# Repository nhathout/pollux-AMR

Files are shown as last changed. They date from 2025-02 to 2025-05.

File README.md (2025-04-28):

# Pollux-AMR · Autonomous Counter-Top Cleaning Robot


> **Last verified:** 27 Apr 2025  
> **Target HW:** Raspberry Pi 4 Model B (4 GB)  
> **Target OS:** Ubuntu 20.04 LTS (headless) with ROS Noetic  

Pollux-AMR is a ROS-driven mobile robot that patrols a kitchen countertop, disinfecting
the surface with a UV-C LED strip while staying clear of cliffs and obstacles.
The original project used a rules-based brain; we now train a real-time PPO agent
on-board via **rl_brain_node.py** for continuous improvement.

---

## 1 · Boot-Up  
    ① Flash Ubuntu 20.04 to the µSD card, boot once to expand the FS
    ② SSH in and run:
    git clone https://github.com/nhathout/pollux-AMR.git
    cd pollux-AMR
    chmod +x setup_env.sh && ./setup_env.sh
    ③ Reboot (systemd service now auto-starts every node)

*Need only a demo video?*
- Links to video demonstrations of Pollux's major functionalities (UV indicator LED, cliff detection, and obstacle avoidance):
    - **UV indication & cliff detection:** [click here](https://drive.google.com/file/d/1kTDrHVp9VE7UjMdm_vTjpf8ZEP2LUoZp/view?usp=sharing)
    - **Obstacle Avoidance:** [click here](https://drive.google.com/file/d/1ax3cWRlPb4nttXV8eBDei8ND6SfjERsN/view?usp=sharing)<br><br>

---

## 2 · Current State (Apr 2025)

| Sub-system | Status | Gotchas & Quirks |
|---|---|---|
| Sensor I/O (hw_publisher.py & hw_publisher_2.py) | ✅ stable | Uses **BCM** pin numbers; wrong ECHO wiring can fry GPIOs. |
| Motor driver (motor_cmd_node.py) | ✅ stable | H-bridge inrush >1 A; keep a 2 A buck or Pi browns out. |
| LED safety (led_gyro_node.py) | ✅ stable | IMU IRQ sometimes locks; power-cycle to clear. |
| RL brain (rl_brain_node.py) | 🟡 beta | Seems to work and learn; first 100 s policy is random. |
| Service file (pollux-robot.service) | ✅ stable | Update **WorkingDirectory=** if you move the repo. |

---

## 3 · Things We Wish We Knew Earlier
1. Ultrasonic crosstalk → fire downward sensors 50 ms apart.  
2. RAM-starved RL → set SWAP = 1024 MB.  
3. Clock drift hurts reward timer → run *timedatectl set-ntp true*.  
4. Wi-Fi sleep kills SSH → set *wifi.powersave = 2* in NetworkManager.  
5. The best power supply for the job.

---

## 4 · Recommended Next Steps

| Area | Content |
|---|---|
| Mechanical | Switch to 12 V steppers for torque & battery life. |
| CV / DL | Add Pi Cam 3 + YOLO-Nano for obstacle detection. |
| DevOps | Stream TensorBoard via MQTT → Grafana. |
| Research | 24 h on-board RL study → short research paper. |

---

## 5 · Directory Map
    pollux-AMR/
    ├─ hardware/
    ├─ images/
    ├─ nodes/
    │   ├─ hw_publisher.py
    │   ├─ hw_publisher_2.py
    │   ├─ motor_cmd_node.py
    │   ├─ led_control_node.py
    │   ├─ led_gyro_node.py
    │   └─ rl_brain_node.py
    ├─ launch/
    ├─ models/
    ├─ scripts/
    └─ systemd/

---

## 6 · Further Reading  
> DISCLAIMER: Some links and documents may require BU account to view.

Software stack → README_SOFTWARE.md  
Hardware build → README_HARDWARE.md  

User Manual → [click here](https://docs.google.com/document/d/1WDNQtBAzQioiVHYzoj2xVuRMR3jV1yGgZe9JvNC5dmk/edit?usp=sharing)<br><br>

Customer Installation Report → [click here](https://docs.google.com/document/d/1myD4TDwbz6tZQjw0WgdVfFCGG7cAGCFSI_ILjvoBSKc/edit?usp=sharing)

Final Test Plan & Report → [click here](https://docs.google.com/document/d/1nLfvciRge8nUAEQmeBG3rHHYXOoPHTD_1vJB__G8N-4/edit?usp=sharing)

*Winning* Shark Tank Video → [click here](https://drive.google.com/file/d/1ElmvJo_tTRmPK1KgQrT9eFHeo6qOJTg3/view?usp=sharing)

Critical Design Review (CDR) Presentation → [click here](https://docs.google.com/presentation/d/1PCzo8z48-ifrknA4HLdUseuIMsqwAZrbvwXN47jLewY/edit?usp=sharing)

Shark Tank Presentation → [click here](https://docs.google.com/presentation/d/1J7x6Hkm6MfULzXxtW8gPblj4HMrZ-OuL5eKAxO-fepI/edit?usp=sharing)

2nd Prototype Test Report → [click here](https://docs.google.com/document/d/1qSaTDLb16L1KKv8wPwOk-qygIFx6U2V5G-Wa-tfIYAA/edit?usp=sharing)

1st Prototype Test Report → [click here](https://docs.google.com/document/d/1bSMtuGWDiYZbLjaCkalLF-rUq3OvFMxzeYqiuovF3EY/edit?usp=sharing)

Preliminary Design Review (PDR) Presentation → [click here](https://docs.google.com/presentation/d/1AgygkBsC4uNbJwVAmwFr3u0lZS7qua3f1DQ_0c6GlmY/edit?usp=sharing)

---

## 7 · License  
MIT License — © 2025 Pollux-AMR contributors

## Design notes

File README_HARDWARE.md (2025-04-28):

# Pollux-AMR · Hardware Report  
_Last updated: 27 Apr 2025_

---

## 1 · Overview  
Pollux-AMR is an autonomous countertop-cleaning robot that:  

* **Detects cliffs** (counter-top edges) with three downward-facing HC-SR04 sensors.  
* **Avoids obstacles** with two forward-facing HC-SR04 sensors.  
* **Performs UV-C sanitation** via an LED strip that is automatically disabled if the robot tilts.  
* **Runs untethered** on a Raspberry Pi 4 Model B (Ubuntu 20.04 headless, ROS Noetic).

---

## 2 · Hardware Components  

| Sub-assembly | Notes |
|---|---|
| **Robot base** | Two DC gearmotors for drive, one caster for balance, 3-D-printed chassis. |
| **Ultrasonic array** | 3 × downward (cliff) + 2 × forward (obstacle). |
| **IMU** | Adafruit MPU-6050 accelerometer / gyroscope (I²C). |
| **LED subsystem** | UV-C strip for sanitation + indicator LEDs. |
| **Drive electronics** | Dual H-bridge; controlled by `motor_cmd_node.py`. |
| **Compute** | Raspberry Pi 4 (4 GB RAM) running all ROS nodes. |

---

## 3 · Power Requirements  

| Rail | Voltage | Typical Current | Source |
|---|---|---|---|
| 5 V (logic / UV-C) | 5 V DC | 1 A | USB-C PSU (3 A headroom) |
| Motor rail | 6 – 12 V | 0.8 – 1.5 A (startup) | External DC boost / Li-ion pack |

> **Hint:** Brown-outs during motor spin-up are the #1 cause of random Pi resets—use separate supplies or a 2 A buck converter.

---

## 4 · Setup Instructions  

1. **Mount ultrasonic sensors** – three downward at the front edge, two forward on the bumper.  
2. **Wire the MPU-6050** – SDA to GPIO 2, SCL to GPIO 3, 3V3 & GND to Pi header.  
3. **Install motors & driver** – connect IN1/IN2/ENA/ENB to Pi GPIOs as specified in `motor_cmd_node.py`.  
4. **Connect LEDs** – UV-C strip to FET driver (GPIO 18 PWM), status LEDs to GPIO 23/24.  
5. **Final assembly** – secure wiring, tape battery, snap lid; verify nothing protrudes below chassis.

---

## 5 · Schematics, PCB & CAD  

**CAD renders**
 
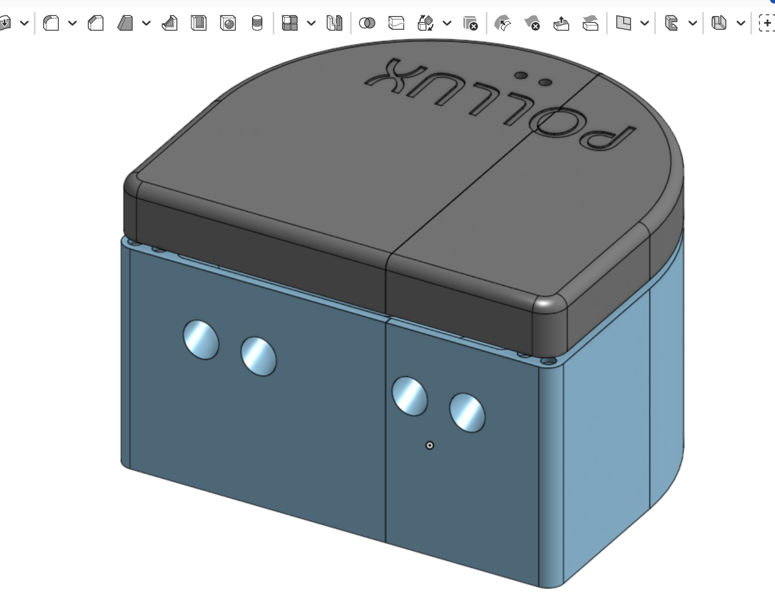
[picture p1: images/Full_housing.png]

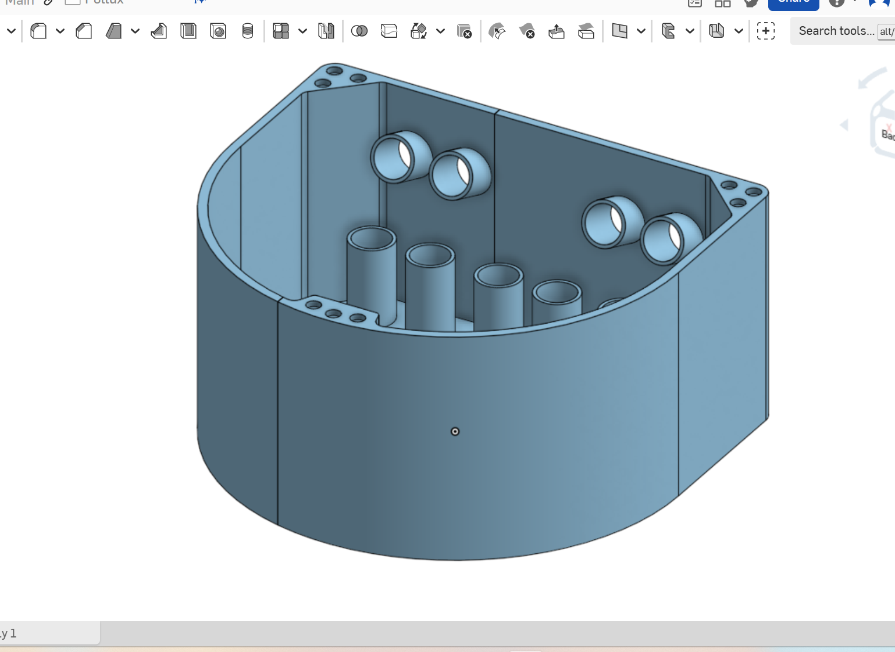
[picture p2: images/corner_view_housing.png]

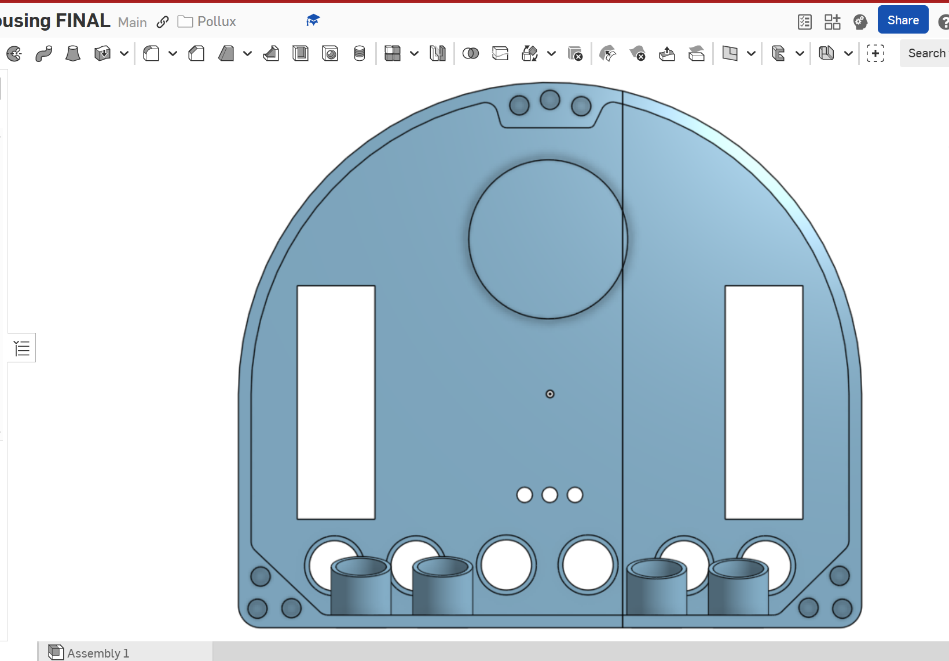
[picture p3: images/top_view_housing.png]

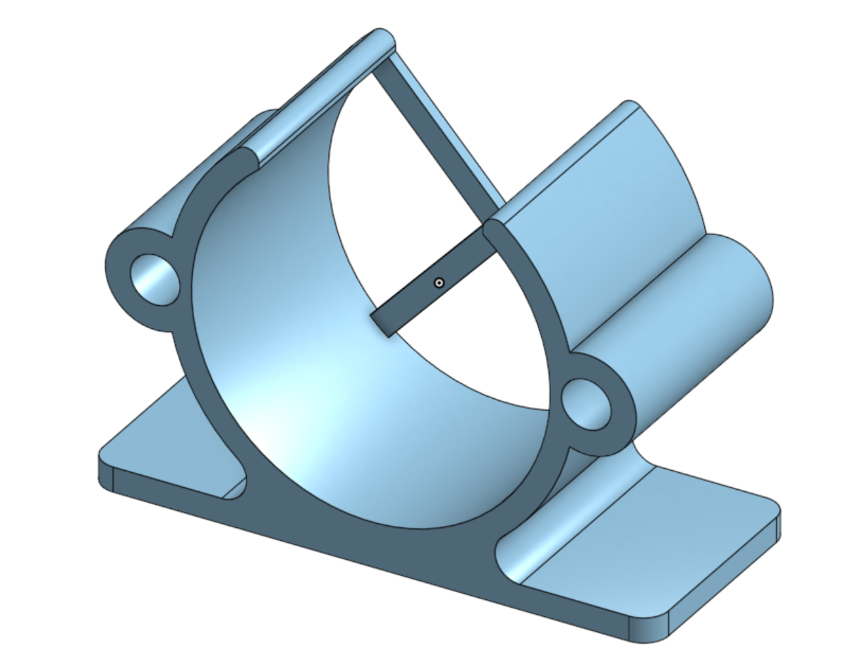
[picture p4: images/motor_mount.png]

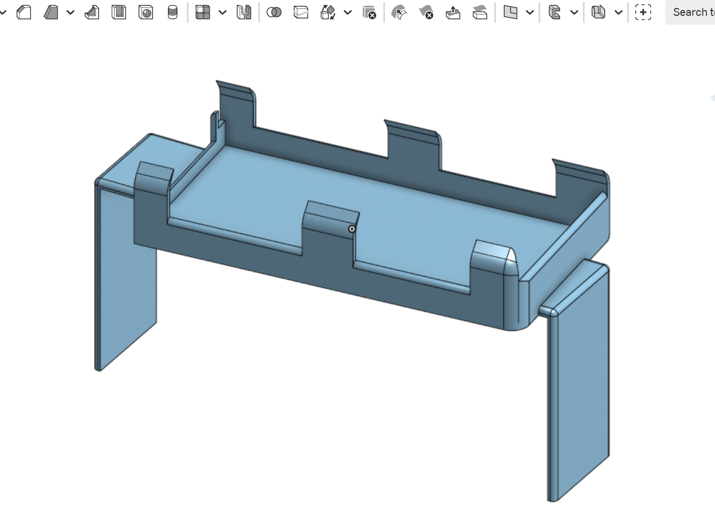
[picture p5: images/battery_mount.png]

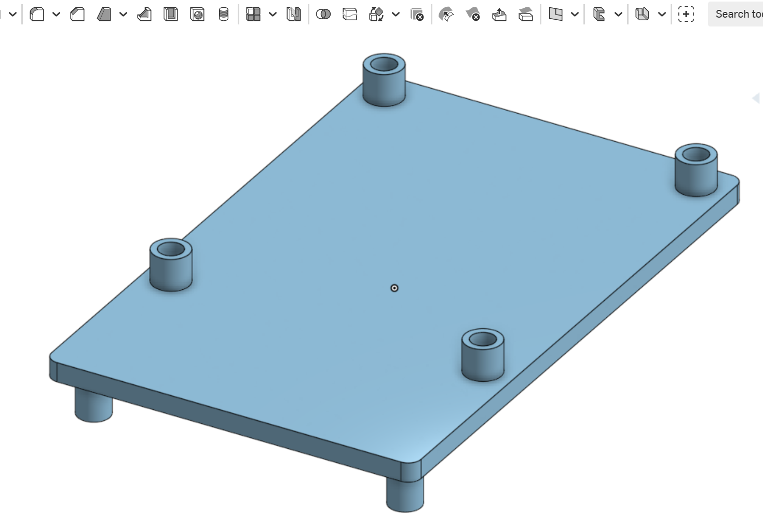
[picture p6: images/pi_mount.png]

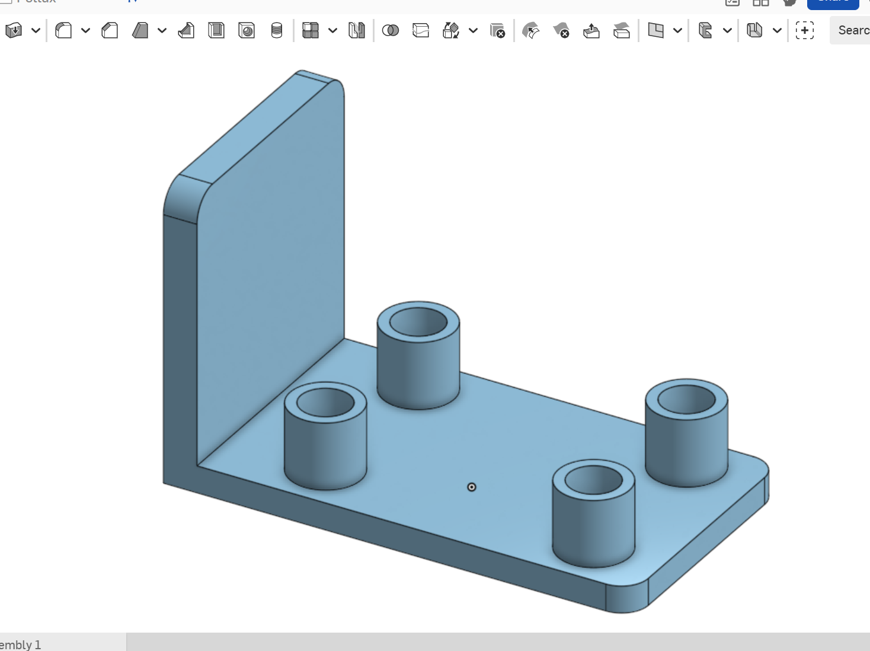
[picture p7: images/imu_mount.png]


**Downloadable STEP files:**  

* [Final Housing](hardware/Final_housing.step)  
* [Motor Mount](hardware/Motor_mount.step)  
* [Battery Mount](hardware/Battery_mount.step)  
* [Pi Mount](hardware/PI_mount.step)  
* [IMU Mount](hardware/IMU_mount.step)

**3-D-printed layout**

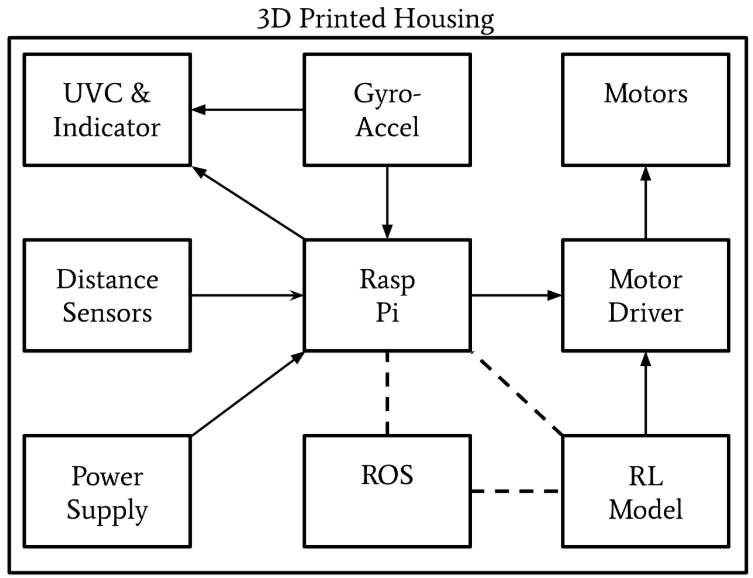
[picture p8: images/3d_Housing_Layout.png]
Housing layout


*Complete KiCad schematics* are in **PDF/**, and Gerbers plus board files in **PCB/**.

---

## 6 · Bill of Materials (Beta build)

| # | Part | Vendor | Qty | Unit $ | Ext $ |
|:-:|---|---|:---:|:---:|:-----:|
| 1 | HC-SR04 ultrasonic | Generic | 5 | 2 | 10 |
| 2 | MPU-6050 IMU | Adafruit | 1 | 15 | 15 |
| 3 | DC gear-motor | Generic | 2 | 3 | 6 |
| 4 | Raspberry Pi 4 (4 GB) | Raspberry Pi Foundation | 1 | 45 | 45 |
| 5 | 8 mW UV-C LED | Amazon | 5 | 12 | 60 |
| 6 | Li-ion battery pack | Energizer | 1 | 40 | 40 |
| 7 | Drive wheels | Amazon | 2 | 1 | 2 |
| 8 | Caster wheel | Amazon | 1 | 2 | 2 |
| 9 | Neodymium magnets | Amazon | 18 | 0.20 | 3.60 |
| 10 | PETG filament | Amazon | 1 | 15 | 15 |

**Total (Beta)**  ≈ **$198.60**

---

## 7 · System Photos  

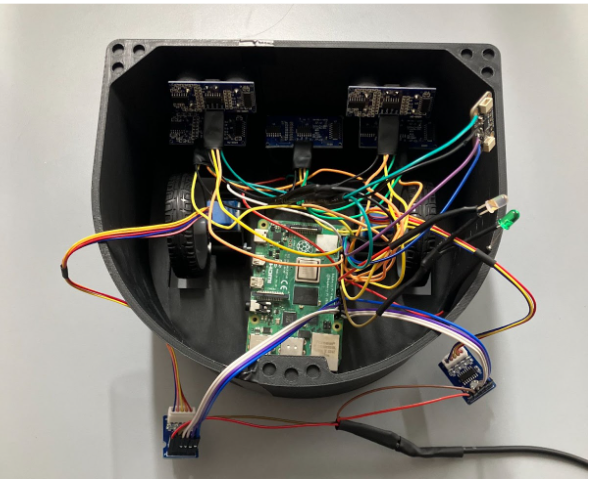
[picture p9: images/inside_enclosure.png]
Inside enclosure
  
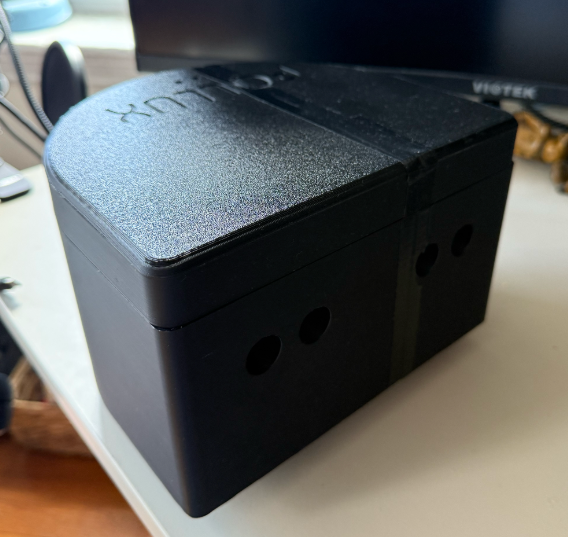
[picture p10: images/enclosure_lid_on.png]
Lid on


---

## 8 · Reference Materials  

* User Manual - [click here](https://docs.google.com/document/d/1WDNQtBAzQioiVHYzoj2xVuRMR3jV1yGgZe9JvNC5dmk/edit?usp=sharing)
* Final Test Plan & Report - [click here](https://docs.google.com/document/d/1nLfvciRge8nUAEQmeBG3rHHYXOoPHTD_1vJB__G8N-4/edit?usp=sharing)

* HC-SR04 Datasheet – <https://cdn.sparkfun.com/datasheets/Sensors/Proximity/HCSR04.pdf>  
* MPU-6050 Datasheet – <https://invensense.tdk.com/wp-content/uploads/2015/02/MPU-6000-Datasheet1.pdf>  
* Raspberry Pi 4 Documentation – <https://www.raspberrypi.org/documentation/>

---

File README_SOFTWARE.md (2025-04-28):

# Pollux-AMR · Software Report  
*Version 2.0 — 27 Apr 2025*

## Table of Contents
1. Module overview  
2. Dependency graph  
3. Dev & build toolchain  
4. Fresh install  
5. Runtime operations   
6. Future improvements
7. Appendix

---

## 1 · Module Overview

| Node / Module | Purpose | Key details |
|---|---|---|
| hw_publisher.py | Publishes /pollux/imu & /pollux/ultrasonic_hw | RPi-GPIO, smbus2, 30 Hz |
| hw_publisher_2.py | Publishes /pollux/ultrasonic_2 | RPi-GPIO, smbus2, 30 Hz |
| motor_cmd_node.py | Drives H-bridge from /pollux/motor_cmd | PWM 1 kHz, watchdog |
| led_control_node.py | Controls UV & status LEDs | ROS service /led_mode |
| led_gyro_node.py | Shuts UV when |roll|>15° | Subscribes /pollux/imu |
| rl_brain_node.py | PPO agent, train/infer | Stable-Baselines3 3.5.0 |
| pollux-robot.service | systemd unit | — |

---

## 2 · Dependency Graph
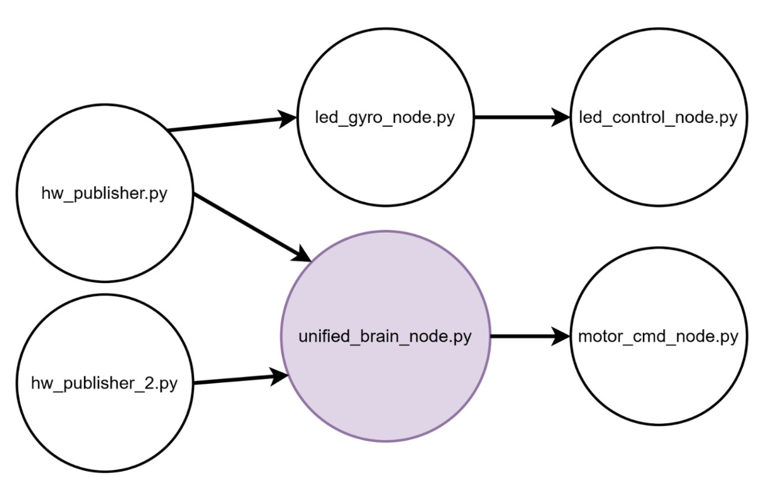
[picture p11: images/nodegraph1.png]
node graph 1

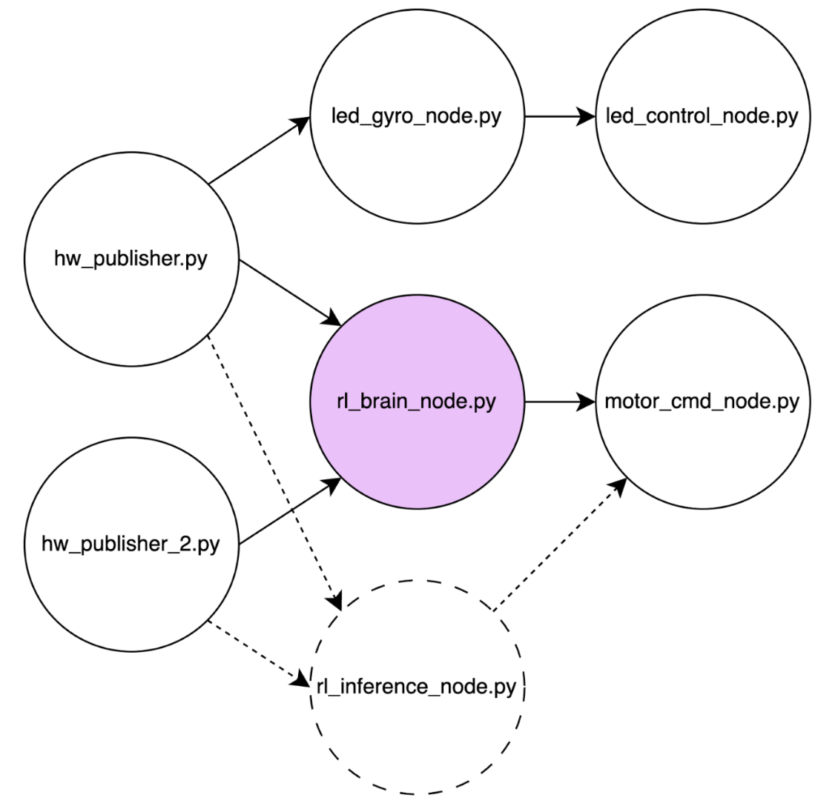
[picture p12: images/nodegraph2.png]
node graph 2


---

## 3 · Dev & Build Toolchain

| Layer | Version | Notes |
|---|---|---|
| OS | Ubuntu 20.04.6 arm64 | CMA = 512 MB |
| Kernel | 5.15.0-1040-raspi | — |
| ROS | Noetic 1.16.0 | — |
| Python | 3.10.12 | - |
| Stable-Baselines3 | 3.5.0 | PyTorch 2.1.0 CPU |
| Gymnasium | 0.29.1 | — |
| CMake | 3.28.1 | optional motor lib |
| CI | GitHub Actions | lint + tests |

---

## 4 · Fresh Install

### 4.1 · Pi Imaging  
Flash *ubuntu-20.04.6-preinstalled-server-arm64+raspi.img.xz*, enable SSH, set hostname *pollux*.

### 4.2 · Base Packages
    ```
    sudo apt update && sudo apt upgrade -y
    sudo apt install -y ros-noetic-ros-base python3-rosdep \
        python3-rosinstall python3-rosinstall-generator \
        python3-wstool build-essential
    sudo rosdep init && rosdep update
    ```

### 4.3 · Project Stack  
    ```
    git clone https://github.com/<your-org>/pollux-AMR.git
    cd pollux-AMR
    chmod +x setup_env.sh && ./setup_env.sh
    ```
*(script installs Python deps, udev rules, enables pollux-robot.service)*

---

## 5 · Runtime Operations

| Mode | Command | Description |
|---|---|---|
| Auto-start | sudo systemctl enable --now pollux-robot | Boots nodes; logs via *journalctl -u pollux-robot -f* |
| Manual | roslaunch pollux_amr all.launch | Same node set, easier debugging |
| RL Train | rosrun pollux_amr rl_brain_node.py --train | Saves model every 5 min |
| RL Infer | rosrun pollux_amr rl_brain_node.py --infer ~/models/best.zip | Low RAM |

---

## 6 · Future Improvements  
* ONNX Runtime for faster inference  
* pigpio waveforms for non-blocking ultrasonic timing  
* ROS dynamic-reconfigure for live tuning  
* GitOps OTA via fluxcd

---

## 7 · Appendix

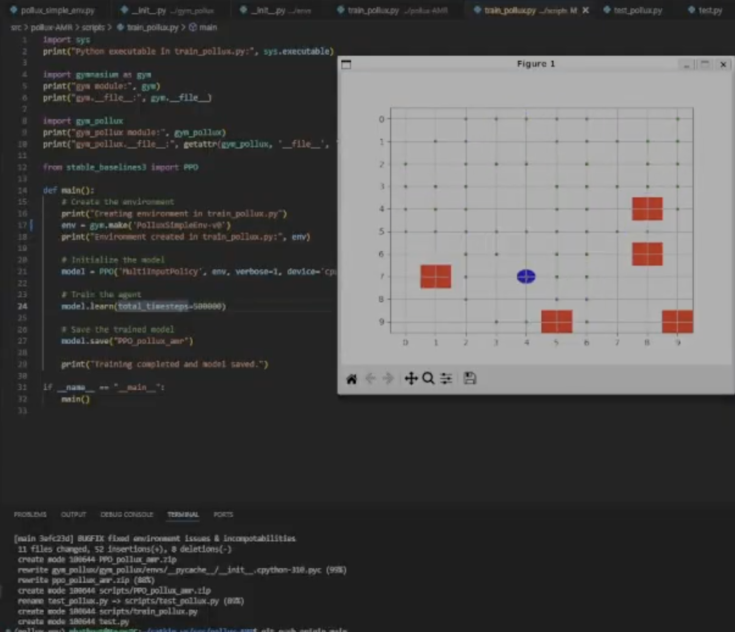
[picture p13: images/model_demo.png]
Press Here to watch the RL model work in simulation! (https://drive.google.com/file/d/1HToGHO0mSNwZyYFLXsZBkUujIVhTotNM/view?usp=sharing)

**Media 1:** The linked clip showcases our custom reinforcement learning model operating within a custom simulation environment rendered using matplotlib. In the video, the agent successfully avoids falling off cliffs and colliding with obstacles, all while effectively exploring and covering roughly 40-60% of the available surface area. The specifics of the model are explained in more detail in our "Supporting Documents" section above.<br><br>

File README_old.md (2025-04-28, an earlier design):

# pollux-AMR
<br>
An autonomous countertop‑cleaning robot designed to avoid falling off edges (“cliffs”) and colliding with obstacles. Pollux‑AMR uses multiple ultrasonic sensors, an IMU, and ROS Noetic to orchestrate all hardware and software interactions. The system can optionally incorporate reinforcement learning for more advanced navigation or policy‑based behaviors.

## Features
- **5× Ultrasonic Sensors**  
  - **3× Downward‑facing** to detect countertop edges (cliffs).  
  - **2× Forward‑facing** for obstacle avoidance.  
- **IMU‑Based LED Control**  
  - Uses gyro/accelerometer data to enable or disable a UV sanitizing LED strip when tilt or angular velocity is unsafe.  
- **ROS Noetic Integration**  
  - Sensor data is published via dedicated hardware publisher nodes.  
  - Motor commands and LED operations are handled by specialized nodes.  
- **Reinforcement Learning (Optional)**  
  - Can integrate with Stable Baselines3 (PyTorch) if you choose to train/adjust navigation policies.  
- **Headless Ubuntu 20.04 on Raspberry Pi 4**  
  - All ROS nodes run on a Pi 4 Model B, flashed with Ubuntu 20.04 (headless).  
  - SSH in to manage and monitor.  

## Stack Architecture
1. **Python 3.10+** – Main language for scripting and control logic.  
2. **Stable Baselines3 (SB3)** – Reinforcement learning library (optional).  
3. **OpenAI Gymnasium (Gym)** – Standard RL environment interface (optional).  
4. **ROS Noetic** – Message passing and node‑based architecture for sensor/control pipelines.  
5. **Development Environment** – Typically remote (SSH) from a Mac/PC into the Pi (Ubuntu 20.04).

## Hardware Components
1. **Robot Base**  
   - 2 motorized wheels, 1 castor wheel, platform for mounting sensors.  
2. **Adafruit MPU‑6050 (6‑DOF)**  
   - Accelerometer + gyroscope for orientation, tilt, and motion data.  
3. **5× HC‑SR04 Ultrasonic Sensors**  
   - 3x downward for cliff detection (pins assigned in `hw_publisher.py`).  
   - 2x forward for obstacle avoidance (pins assigned in `hw_publisher_2.py`).  
4. **LED Sub‑System**  
   - A UV LED strip for surface sanitation, plus indicator LEDs; controlled via `led_control_node.py` + `led_gyro_node.py`.  
5. **Stepper Motors and Drivers**  
   - Controlled by `motor_cmd_node.py` using a DualMotorController.  
6. **Raspberry Pi 4 Model B (4GB)**  
   - Core computing platform (ARM Cortex‑A72), 4× USB ports, WiFi, GPIO pins for sensors/motors, runs ROS nodes headlessly.

## Setup
- **Clone the Repo**
  ```bash
   git clone https://github.com/nhathout/pollux-AMR.git
   cd pollux-AMR
  ```
- **Install Dependencies**
  - ROS Noetic: Follow the official ROS installation guide for Ubuntu 20.04.
  - Required packages (assuming ROS2 Noetic installed at ```/opt/ros/noetic``` and you have a ```catkin_ws``` at ```~/catkin_ws```):
    ```bash
    chmod +x setup_env.sh
    ./setup_env.sh
    ```
- **Install Custom Gym Environment**
  - ```bash
    pip install -e gym_pollux
    ```

## Supporting Documents & Media
(MAY REQUIRE BU ACCOUNT TO VIEW)
- Link to **User's Manual:** [click here](https://docs.google.com/document/d/1WDNQtBAzQioiVHYzoj2xVuRMR3jV1yGgZe9JvNC5dmk/edit?usp=sharing)<br><br>

- Links to video demonstrations of Pollux's major functionalities (UV indicator LED, cliff detection, and obstacle avoidance):
    - **UV indication & cliff detection:** [click here](https://drive.google.com/file/d/1kTDrHVp9VE7UjMdm_vTjpf8ZEP2LUoZp/view?usp=sharing)
    - **Obstacle Avoidance:** [click here](https://drive.google.com/file/d/1ax3cWRlPb4nttXV8eBDei8ND6SfjERsN/view?usp=sharing)<br><br>

- Links to video demonstrations of Pollux's major functionalities (UV indicator LED, cliff detection, and obstacle avoidance):
    - **UV indication & cliff detection:** [click here](https://drive.google.com/file/d/1kTDrHVp9VE7UjMdm_vTjpf8ZEP2LUoZp/view?usp=sharing)
    - **Obstacle Avoidance:** [click here](https://drive.google.com/file/d/1ax3cWRlPb4nttXV8eBDei8ND6SfjERsN/view?usp=sharing)<br><br>

- Link to **Final Test Plan & Report:** [click here](https://docs.google.com/document/d/1nLfvciRge8nUAEQmeBG3rHHYXOoPHTD_1vJB__G8N-4/edit?usp=sharing)
- Link to **(winning) Shark Tank Video:** [click here](https://drive.google.com/file/d/1ElmvJo_tTRmPK1KgQrT9eFHeo6qOJTg3/view?usp=sharing)
- Link to **Critical Design Review (CDR) Presentation:** [click here](https://docs.google.com/presentation/d/1PCzo8z48-ifrknA4HLdUseuIMsqwAZrbvwXN47jLewY/edit?usp=sharing)
- Link to **Shark Tank Presentation:** [click here](https://docs.google.com/presentation/d/1J7x6Hkm6MfULzXxtW8gPblj4HMrZ-OuL5eKAxO-fepI/edit?usp=sharing)<br><br>
  
- Link to **2nd Prototype Test Report:** [click here](https://docs.google.com/document/d/1qSaTDLb16L1KKv8wPwOk-qygIFx6U2V5G-Wa-tfIYAA/edit?usp=sharing)
- Link to **Prototype Test Report:** [click here](https://docs.google.com/document/d/1bSMtuGWDiYZbLjaCkalLF-rUq3OvFMxzeYqiuovF3EY/edit?usp=sharing)
- Link to **Preliminary Design Review (PDR) Presentation:** [click here](https://docs.google.com/presentation/d/1AgygkBsC4uNbJwVAmwFr3u0lZS7qua3f1DQ_0c6GlmY/edit?usp=sharing)

## Contributing
Please feel free to open GitHub Issues, feature requests, and pull requests :)

## Appendix
[![Press Here to watch the RL model work in simulation!](/images/model_demo.png)](https://drive.google.com/file/d/1HToGHO0mSNwZyYFLXsZBkUujIVhTotNM/view?usp=sharing)
**Media 1:** The linked clip showcases our custom reinforcement learning model operating within a custom simulation environment rendered using matplotlib. In the video, the agent successfully avoids falling off cliffs and colliding with obstacles, all while effectively exploring and covering roughly 40-60% of the available surface area. The specifics of the model are explained in more detail in our "Supporting Documents" section above.<br><br>

<img src="/images/trained.png" alt="trained" width="40%"><br>
**Figure 1:** Successful model trained on the Raspberry Pi to prove ability to dynamically train on a Pi 4 Model B.

## License 
This Project is licensed under the MIT License. You are free to modify and distribute this code under those terms.

## Other (Dev) Notes:
- Raspberry Pi flashed with Ubuntu 20.04 LTS (headless)
- ROS Noetic successfully installed
- SSH from a Mac to the Pi for remote development
- **To change the WiFi network** that the Pi tries to connect to automatically:<br>
  - ```sudo vim /etc/netplan/50-cloud-init.yaml```<br>
  - Change the SSID and password, then apply changes:<br>
  - ```sudo netplan apply```<br>

  - **Verifying Connection:**
       - ```ip addr show wlan0```
       - ```ping google.com```

## Getting Started:
just turn on the Pi!
(added script to our Pi that runs all the ros nodes below)

Note: use ```journalctl -u pollux-robot.service -f``` for live logging details when SSHing<br>
OR Run all nodes in the foreground with roslaunch: ```roslaunch pollux_amr all.launch```

<br><br><br>
*Running Everthing (legacy test unless using your own RaspPi)* <br>
IMPORTANT Reminder: whenever SSHing into the Raspberry Pi, to utilize ROS and ROS nodes, you must:<br>
- ```cd catkin_ws/```<br>
- ```catkin_make```<br>
- ```source devel/setup.bash```<br>

1. Terminal 1:<br>
   ```roscore```<br>

2. Terminal 2:<br>
   ```rosrun pollux_amr hw_publisher.py```<br>

3. Terminal 3:<br>
   ```rosrun pollux_amr motor_cmd_node.py```<br>

4. Terminal 4:<br>
   ```rosrun pollux_amr brain_node.py```<br>
<br><br>
*Running ROS (legacy test)*
1. Open a terminal (SSHed into the Pi) and run:<br>
   ```roscore```

2. In another terminal, run the hardware publisher node:<br>
   ```rosrun pollux_amr hw_publisher.py```

   - To check sensor data:<br>
      ```rostopic echo /pollux/imu```<br>
      ```rostopic echo /pollux/ultrasonic_hw```

3. For motors:<br>
   ```rosrun pollux_amr motor_cmd_node.py```

   - To publish a command (move the motors):<br>
      ```rostopic pub /pollux/motor_cmd std_msgs/Int32 "data: 0"``` (0 is an attempt to move forward)

*To run individual HW tests on the Pi without ROS (legacy tests):*
- ```python3 -m pollux-AMR.hardware.tests.test_imu```
- ```python3 -m pollux-AMR.hardware.tests.test_ultrasonic```
- ```python3 -m pollux-AMR.hardware.tests.test_motors``` (crashes/reboots Pi; I think due to too much power consumption by the motors)

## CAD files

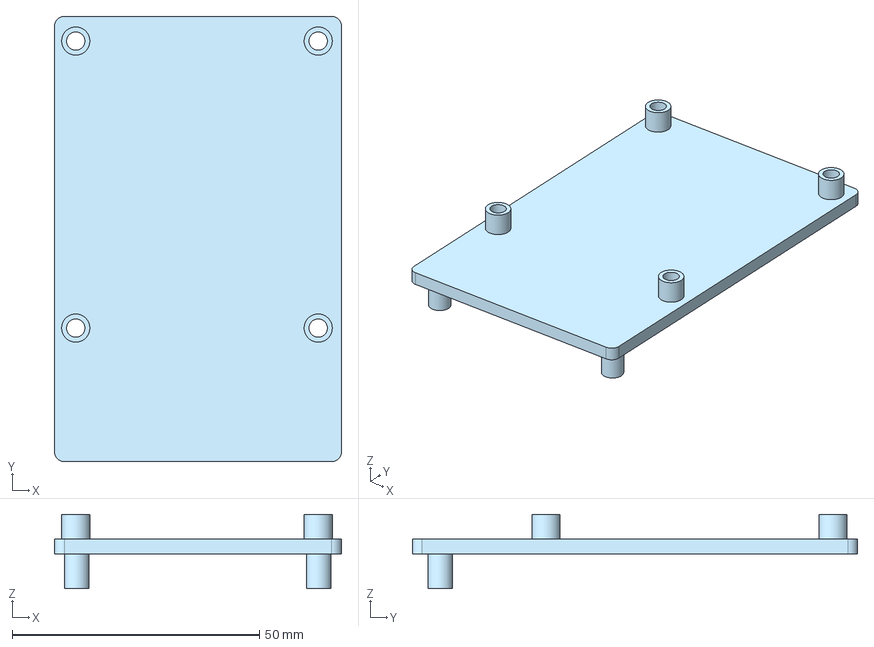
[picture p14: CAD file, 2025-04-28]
hardware/PI_mount.step
58.0 x 90.0 x 15.0 mm

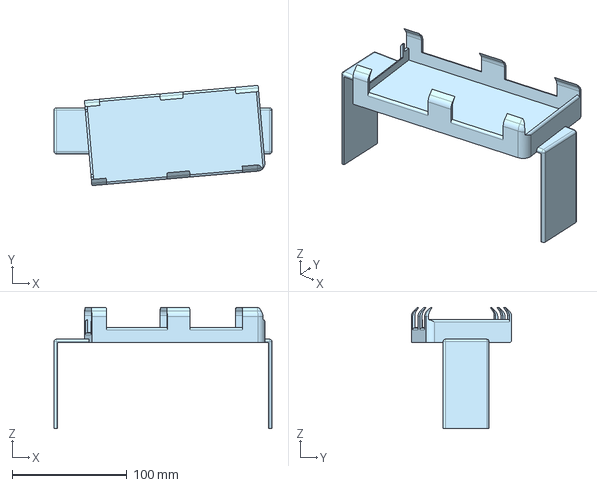
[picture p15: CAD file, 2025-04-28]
hardware/Battery_mount.step
190.0 x 87.5 x 105.8 mm

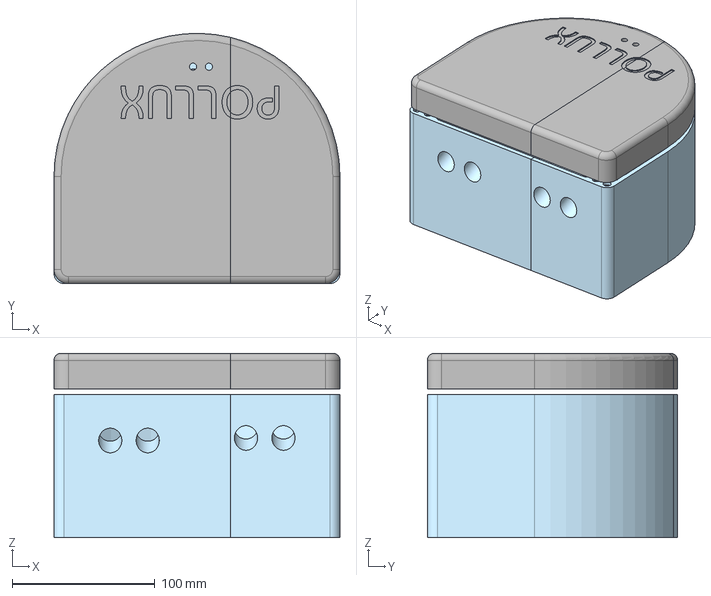
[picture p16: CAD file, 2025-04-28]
hardware/Final_housing.step
200.0 x 175.0 x 129.0 mm

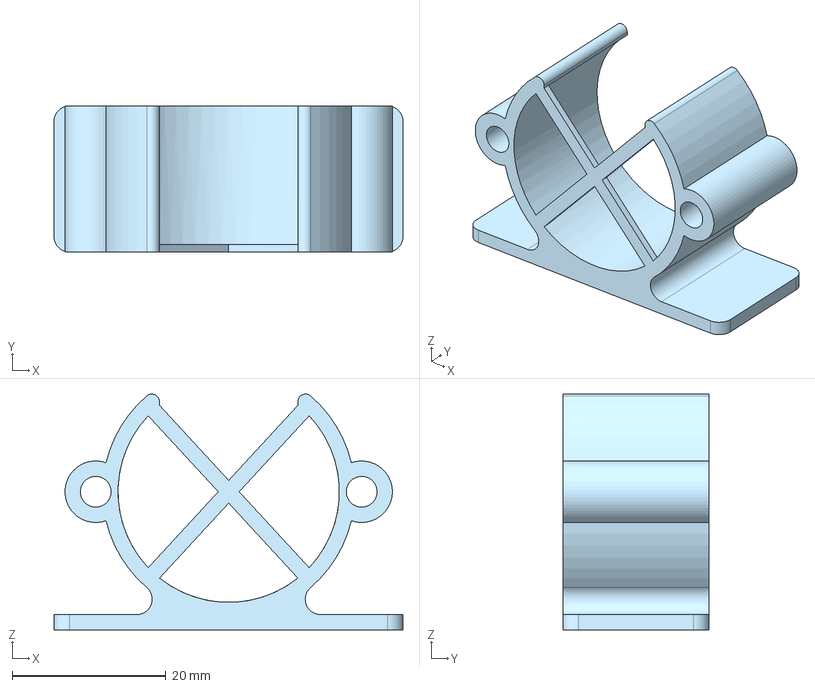
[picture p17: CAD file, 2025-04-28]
hardware/Motor_mount.step
45.4 x 19.0 x 30.7 mm

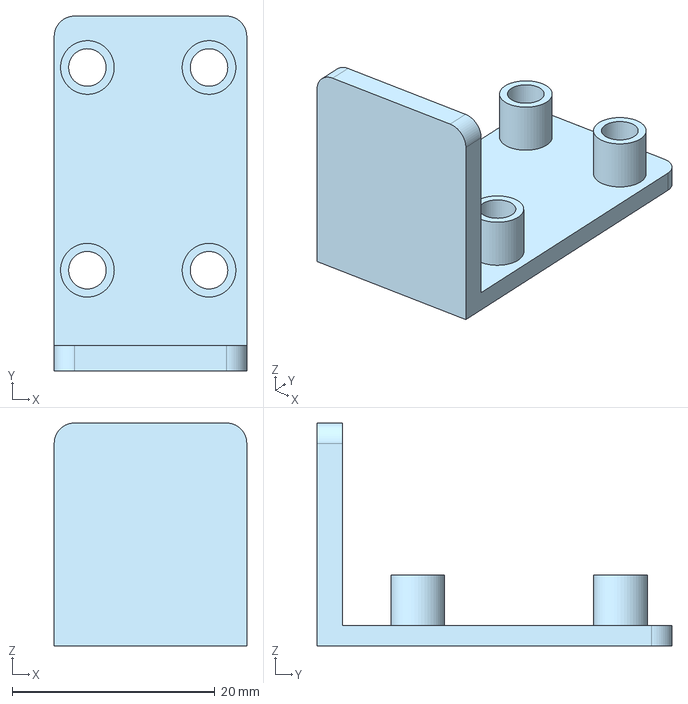
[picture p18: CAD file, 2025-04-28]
hardware/IMU_mount.step
19.0 x 35.0 x 22.0 mm

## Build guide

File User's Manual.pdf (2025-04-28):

## Boston University

## Electrical & Computer Engineering

EC463 Capstone Senior Design Project

## User’s Manual

## Pollux

by Team 22

Wenhao Cao wenhaoc@bu.edu
Karl Carisme karlc@bu.edu
Louis Cicala cicala@bu.edu Noah Hathout nhathout@bu.edu Caelan Wong caewong@bu.edu

Table of Contents

Executive Summary | 2
1 Introduction | 3
2 System Overview and Installation | 4
3 Operation of the Project | 6
4 Technical Background | 7
5 Relevant Engineering Standards | 11
6 Cost Breakdown | 12
7 Appendices | 13

Executive Summary

Maintaining cleanliness in the kitchen is a priority for many, but deep cleaning and sanitizing can be time consuming and involve the use of harmful chemicals that may linger in the environment.

Pollux will be a self-operating countertop cleaning robot, capable of cleaning and disinfecting surfaces without the use of harsh chemicals. Utilizing UV light for sterilization, it will offer a safe and effective alternative to traditional cleaners.

Pollux will autonomously navigate countertops, avoiding obstacles and detecting edges. It will be equipped with UVC diodes capable of killing 99% of germs, and a gyroscopic failsafe mechanism to ensure users can never be exposed to this UV light.

Pollux will provide a convenient, hands-free method to maintain cleanliness, not only in kitchens but on any surface where sanitation is a priority. Ultimately, the Pollux aims to reduce the time and effort users spend on cleaning and absolve users of the usage of harmful chemicals.

### 1 Introduction

Everyone desires cleanliness in their homes, and nowhere else is it as important than in the kitchen. Kitchen surfaces like tables and countertops regularly come into contact with raw or undercooked food, so sanitation becomes imperative once it is understood that these pathogens can cause serious foodborne illnesses.

However, deep cleaning something like a kitchen countertop is an involved task – cleaning at more than face value requires time and consideration. It is easy to wipe down a countertop so it looks clean, but this does not make it truly clean. Unless germs are killed, they may persist, which is highly undesirable in a kitchen.

There is a large consumer market for cleaning products advertised to kill such germs and to make the cleaning process more efficient and effective. However, users may not be aware of the underlying health risks associated with these chemical cleaners. A June 2024 study, “Cleaning Products…” by Salonen et al., found the following:

“The use of cleaning products indoors may increase occupants’ exposure to a variety of harmful environmental pollutants including volatile and semi volatile organic compounds (https://www.sciencedirect.com/topics/pharmacology-toxicology-and-pharmaceutical-science/volatile-organic-compound) (VOCs and SVOCs), particulate matter (PM), and nitrogen dioxide… (https://www.sciencedirect.com/topics/pharmacology-toxicology-and-pharmaceutical-science/nitrogen-dioxide)

household cleaning agents are sensitizers or airway irritants, (https://www.sciencedirect.com/topics/pharmacology-toxicology-and-pharmaceutical-science/irritant-agent) and have been associated with impaired respiratory health among children and adults…

use of products in spray form at home can increase asthma incidence, current asthma, and poorly controlled asthma in adults and wheezing in children” [1]

Considering these issues, there is not only a financial incentive to provide consumers with a time-saving solution to properly clean surfaces, but also legitimate health concerns over how the cleanliness-minded can safely clean surfaces.

Therefore, we built the Pollux: an autonomous countertop cleaning robot that disinfects using UV light. The Pollux saves users both time and effort by cleaning surfaces completely independently, with no input required other than starting the device. Additionally, the Pollux solves the problem of hazardous sanitation products by using a UV light instead of any chemicals and by maintaining separation between the user and the light.

Over the past two semesters, we have developed and implemented these ideas as a team. The result is an easy to use robot that we hope can make a positive impact on household efficiency and safety.

### 2 System Overview and Installation

### 2.1 Overview Block Diagram

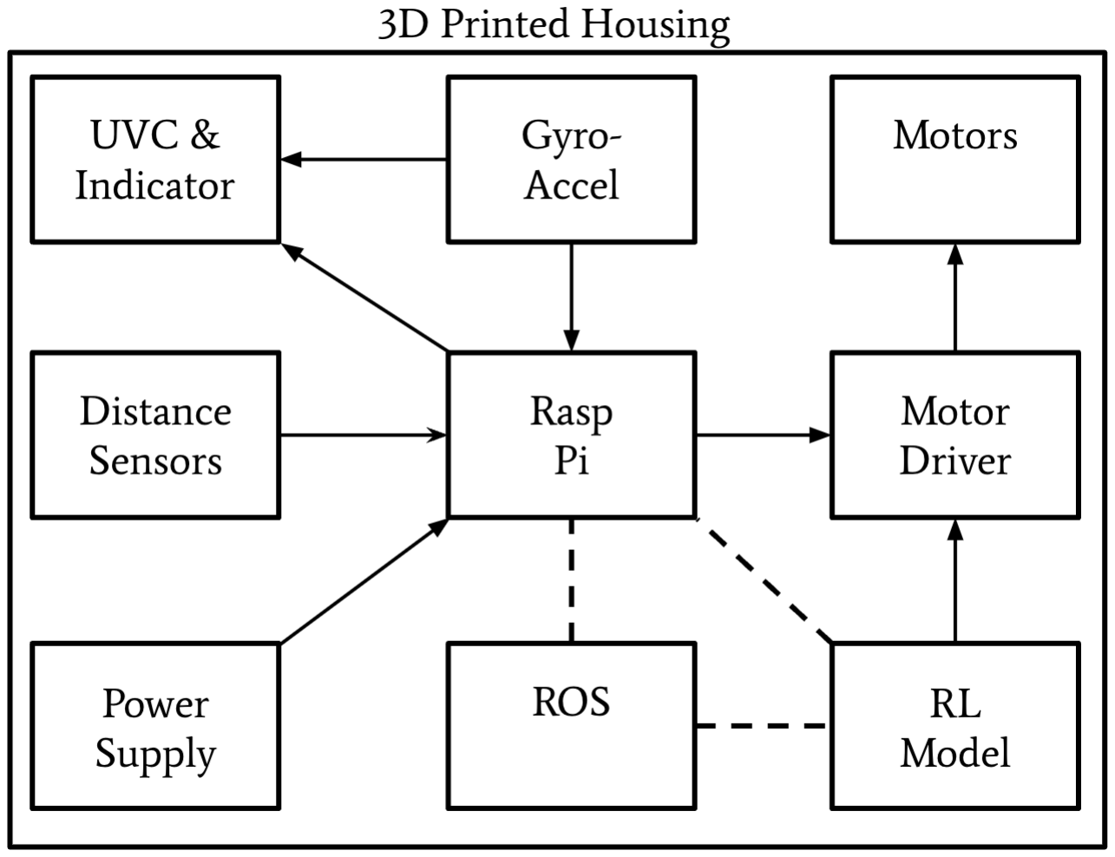
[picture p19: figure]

Figure 2.1.1 – Block diagram representing the major components of the Pollux. Arrows represent hardware components, all of which are powered by the main power supply and all of which connect to the central Raspberry Pi. Dashed lines represent software components, which are further elaborated below.

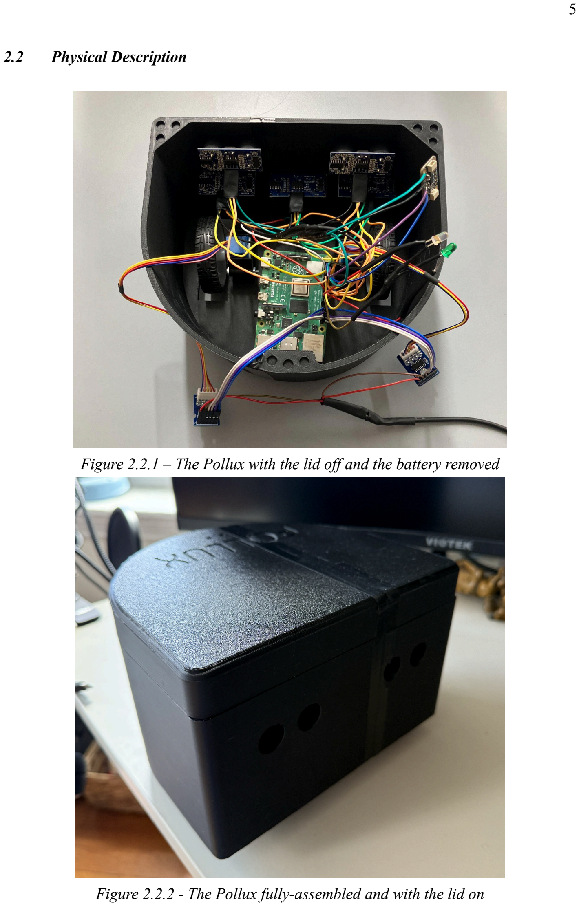
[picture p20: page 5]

### 2.2 Physical Description

Figure 2.2.1 – The Pollux with the lid off and the battery removed

Figure 2.2.2 - The Pollux fully-assembled and with the lid on

### 2.3 Installation, Setup, and Support

No installations are required to make full use of the Pollux. On the robot’s Raspberry Pi is a startup script that, once powered on, runs all required ROS nodes and begins dictating the robot’s movement after a start-up delay of approximately one minute. A simple way to tell when the robot is fully-booted is once the green LED on top of the robot turns on – this LED is an on/off indicator.

To set up and use the Pollux, first ensure that the battery is sufficiently charged. This can be done by removing the lid and pressing the thin button on the side of the battery. This will subsequently display what percentage of the battery remains. Place the Pollux on a surface (countertop, table, etc) and clear off any area that you wish to be sanitized. Then, simply press the power switch on.

The Pollux has been designed for one continuous mode of operation. There is no need to configure anything or interact directly with any software. If you encounter any bugs or strange behavior from the Pollux, first ensure that the battery is sufficiently charged, as the robot may operate slower at low battery. If the battery is not low, turn the Pollux off and turn it back on. This initiates a full reboot – all ROS nodes are terminated and then re-initialized on startup.

### 3 Operation of the Project

### 3.1 Operating Mode 1: Standard Operation

Starting the Pollux
1. Place the Pollux on a level surface
2. Press the power switch to ‘on’
3. Allow up to two minutes for the Pollux to boot

Sanitization
1. The Pollux will move slowly as it sanitizes the surface underneath it
2. The Pollux will turn whenever it reaches an edge or an obstacle
3. The Pollux may also turn if it has not yet reached a barrier
4. If overturned, the LEDs beneath the Pollux will deactivate

Edge detection
1. When the Pollux reaches an edge, it will halt
2. The Pollux will then turn and continue sanitizing in a different direction

Obstacle detection
1. When the Pollux reaches an obstacle, it will halt
2. The Pollux will then turn and continue sanitizing in a different direction

Stopping the Pollux
1. Press the power switch to ‘off’ – the Pollux can be stopped at any point without risk of UV exposure or interference with software

### 3.2 Operating Mode 2: Abnormal Operations

If the Pollux is low on battery, it should be recharged until the battery is full or nearly full. The Pollux may halt movement or shut off altogether when the battery runs low enough.

Although it is unlikely, the reinforcement learning model may instruct the robot to enter a movement loop. If this behavior is observed, simply turn the Pollux off and power it back on in order to reboot it.

### 3.3 Safety Issues

The Pollux is lightweight and moves very slowly, thus the risk of physical injury from the Pollux is slim to none.

Similarly, the Pollux is a low-voltage system, with no component operating at any higher than 5 volts. The internal battery is also short-circuit protected. Hence, the risk of electrical shocks or otherwise electrical injuries is very little.

In its alpha version, the Pollux does not utilize any real UVC diodes – instead, faux LEDs mimic the function of UVC light. In the next iteration of the Pollux, though, real UVC diodes will be implemented, which are hazardous to anyone that contacts the emitted UV light. For this reason, the Pollux contains a gyroscope that turns these LEDs off whenever the robot is overturned, i.e. if someone knocks it over during operation. In the future, quantitative testing will need to be performed to assess how much UV light ‘leaks’ out from underneath the robot – however, our gyroscope system fully prevents direct exposure.

### 4 Technical Background

### 4.1 Robot

The Pollux robot is built around a Raspberry Pi 4B. Connected to the Pi’s GPIO pins are ultrasonic sensors, motor drivers, LEDs, and an accelerometer/gyroscope. The robot essentially serves to take input from the surrounding environment, and output in the form of movement and LED control. The robot moves by making use of two adjacent stepper motors, controlled by the aforementioned motor drivers. Also attached to the underside of the robot is a central caster wheel – when combined with the two motorized wheels, this allows the Pollux to rotate in place and maneuver more effectively in tighter spaces. On top of the robot are two LEDs – one indicates on/off, and the other indicates whether or not the UVC LEDs underneath the robot are on. Then, on the underside of the robot is a strip of three LEDs that stay on whenever the robot is upright, mimicking UV sanitization.

### 4.2 Housing

The housing for the Pollux was custom-designed to securely and efficiently accommodate all the internal components. It was modeled in Onshape and is fully 3D printed. The overall structure features a semi-circular shape, which allows the robot’s edges to better fit into corners and along walls during operation The cured rear of the housing adds a sleek, modern appearance to the device.

To ensure secure assembly, there are 18 embedded magnets between the body and lid. These provide a firm hold, even if the robot is turned upside down. The lid is engraved with the product’s name and includes two LED holes: one as an on/off indicator and the second as a UV light indicator.

Internally, the housing contains a spot for every component. There are precisely modeled compartments for each of the five ultrasonic sensors. There are three located along the bottom front, and two mounted on the front walls. The two front sensors are angled 15 degrees downward for improved object detection. The housing also supports two motor mounts and wheels, a dedicated ledge mount for the IMU (to keep it securely fixed to prevent unnecessary movement), a raspberry pi mounting platform, and a shelf-like battery mount. The battery mount was designed to position the larger battery above other components for optimal space usage.

### 4.3 Robotic Operating System (ROS)

Pollux relies on ROS Noetic as the software backbone, running headlessly on a 64-bit Ubuntu 20.04 image on a Raspberry Pi 4 Model B. All on-board software is divided into numerous ROS nodes that communicate through the standard publisher-subscriber fashion. This allows the sensing, actuation, and decision-making subsystems run concurrently while not depending on each other too much. This modular design keeps the coding, debugging and testing manageable, and allows any one component to be replaced, edited, or added without changing or damaging the rest of the system.

On boot up, a dedicated file on the Pi named “pollux-robot.service” is invoked, where the environment is created for PyTorch to successfully launch. Next, the main ROS launch file, roscore, is ran, which spawns the two ultrasonic-sensor-publishing nodes, the IMU-based LED failsafe, the motor driver, and finally the reinforcement learning controller (“rl_brain_node.py”). There is a few minute delay before the robot launches due to the launching of all the separate nodes, motors, and sensors, but soon after the robot launches user’s are also able to SSH into the robot to access the Pi and kill/run whichever nodes they desire (more detail about this on the project README.md: click here). (https://github.com/nhathout/pollux-AMR)

Sensor data originates from the two “hw_publisher” nodes. The first node publishes the data from three bottom-facing ultrasonic sensors, while the second node publishes two forward-facing ultrasonic sensors. These streams, together with the IMU readings coming from the accelerometer and gyroscope, feed into the reinforcement learning controller’s ROS node. Inside this node (“rl_brain_node.py”) is a Proximal-Policy-Optimization (PPO) network that operates at two hertz and chooses movement commands (forward, backward, left-spin, right-spin, or stop). Its reward function penalizes cliff readings, close front obstacles, excessive horizontal/vertical acceleration that suggest falls, unnecessary backward movement, and idling. On the other hand, the reward function rewards exploratory motion and successful coverage of new ground.

While the brain node controls mobility, the two LED nodes run in parallel. “led_control_node.py” takes in high-level LED commands from the “led_gyro_node.py”, which checks if the IMU reports a tilt beyond a certain threshold, which in turn should turn off the UV LEDs as well as the UV-indicator LED on the top of the robot. Because this safeguard is implemented in a separate ROS node, it can remain on and working even if the learning controller is paused, crashed, or replaced.

Embedding ROS in this way allows for a very straightforward path to upgrades and enhancements. Additional sensors, such as depth cameras or LiDAR, can be added merely by introducing a new publisher node and subscribing to it with a new and improved brain node. Similarly, replacing the PPO policy with another policy would require only editing the reinforcement learning controller’s ROS node, leaving the rest of the robot untouched. Ultimately, this allows Pollux with increased robustness and adaptability to change and enhancements.

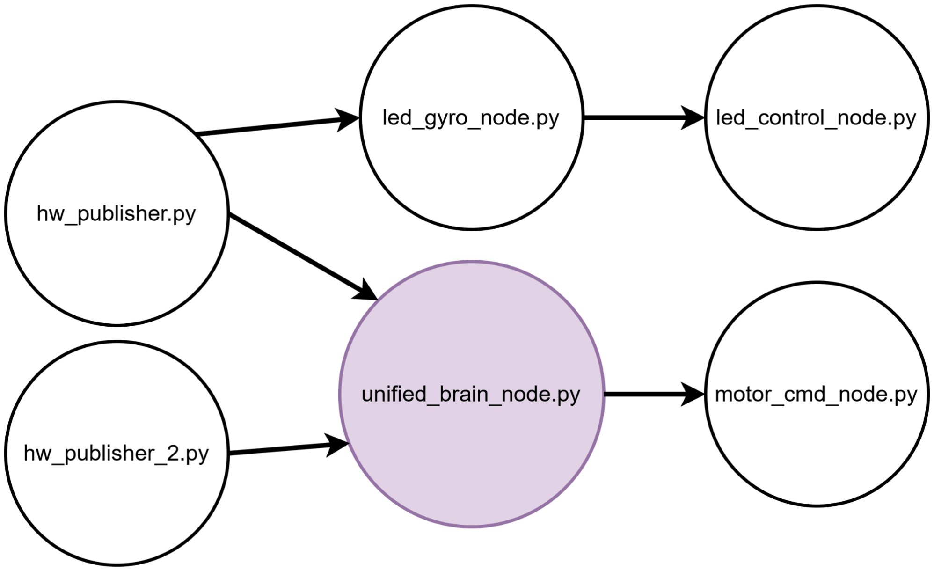
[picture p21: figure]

Figure 4.3.1 – ROS node topology for the classical controller. The diagram shows every ROS node deployed on Pollux when the legacy deterministic brain (“unified_brain_node.py”) is in use. Arrows leaving a node indicate topics that the node publishes; while arrows entering a node indicate topics that the node subscribes to. The hardware publisher nodes provide raw sensor streams, the unified brain node converts those streams into high-level motor and LED commands, and the remaining driver nodes act on those commands real-time.

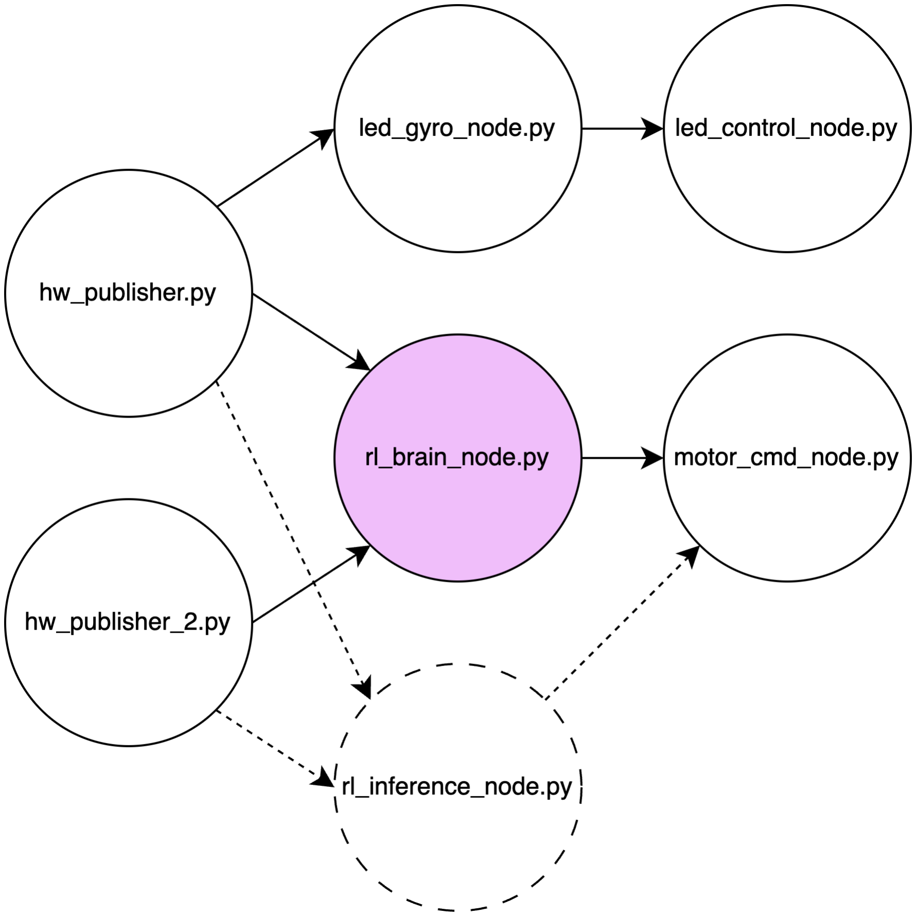
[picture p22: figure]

Figure 4.3.2 – ROS node topology for the reinforcement learning controller. The diagram is identical to Figure 4.3.1 except that the deterministic “unified_brain_node.py” has been replaced by “rl_brain_node.py” or “rl_inference_node.py”, which can operate in training mode, or (once trained), in inference mode. The dashed lines indicate that the node is only run after the model is fully trained by running the RL brain node.

### 4.4 Reinforcement Learning

The autonomous behavior of Pollux is governed by a reinforcement learning (RL) controller that functions as the robot’s “brain.” Its general purpose is to interpret live sensor data, select from a given set of motion commands, and maximize the surface area covered while guaranteeing that obstacles and cliff edges are avoided. The controller uses the Proximal-Policy-Optimization (PPO) algorithm, chosen for its stability on resource-constrained hardware.

When the robot is running, the bottom and front-facing ultrasonic sensors stream five distance measurements every half a second. Concurrently, the on-board IMU supplies linear acceleration in the horizontal plane, as well as angular velocity. These eight values from the continuous observation are given to the agent/robot, where a single pass of these values yields one of the five motor commands: forward, backward, spin-left, spin-right, or stop. Motor commands are then published to the motor command node two times a second.

The reward function is built solely to reward good surface coverage patterns and penalize harmful or inefficient behavior. To begin, there is a small positive reward added every time-step to encourage continuous movement, with an added bonus when data seems to vary, which is an indication that the robot is reaching unexplored territory. Large negative penalties are given to the agent whenever any bottom sensor detects a cliff, whenever the front sensors detect possible collision danger, and whenever the IMU registers acceleration above a certain threshold, indicating a fall or slip. It was necessary to ensure the robot would not move backwards too often, since it could cause the robot to fall off cliffs due to a lack of cliff-detecting sensors located at the back of the robot. To do this, backward motion also penalized the agent unless it happened after detecting an obstacle or cliff. After a lot of training, the shaping of this reward function leads to an agent that learns a sweeping pattern of forward spins interrupted by carefully measured retreats away from cliffs or walls.

Training was done in two stages. The first stage was off-board on a desktop PC, running Ubuntu 20.04, Python 3.10, Stable-Baselines3, and Gymnasium. This stage trained and successfully worked in a simulated environment using MatPlotLib. This model is then taken and improved on by “rl_brain_node.py,” which continues the training on-board, with real-life data.

Because the RL controller is done in a single ROS node, it can be replaced, altered, improved without touching the rest of the software stack. In the future, this feature allows the adaptability to possibly incorporate a depth sensing camera or a LiDAR sensor.

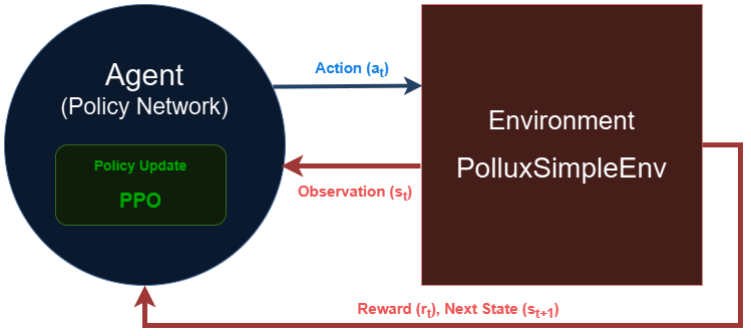
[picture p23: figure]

Figure 4.4.1 – the internal agent-environment interaction, including state representations, rewards, action commands, and other observations

### 5 Relevant Engineering Standards

The most relevant standard for the Pollux is the speed at which it moves. Because the Pollux sanitizes using UV light, it is crucial to ensure that it not only covers as much area as possible, but also that each section of the area it covers receives enough UV light to have a proper germicidal effect.

According to a study from the National Institute of Health, a minimum dose of 27 mJ per cm² of UVC light (222nm) was required for a 99% germicidal effect [2]. We can convert this figure to 27mW*s per cm²
, meaning that a 27 mW UVC diode at a wavelength of 222nm requires a full second to kill 95% of germs on an area of one square centimeter. Alternatively, we say that any wattage is sufficient to kill 95% of germs, so long as the time for which it is exposed results in a sum of 27mW exposed to each square centimeter.

Sourcing safe and effective UVC diodes would be an extensive process, and it is not one that was covered during the development of the Pollux, since it is highly likely that these LEDs would need to be specially designed and ordered. However, “A critical review of ultra-violet light emitting diodes…” by Rauch et al provides insight into the strength of UVC LEDs that could be expected. Rauch et al note that the average price point of UVC LEDs between 265 and 280 nm is $1466 USD per W²

, the same as $1.466 USD per mW² [3].

Assume that the Pollux Beta Version will contain a strip of five LEDs on the bottom. In order to maintain a cost of around $200, there is a surplus of roughly $60 for these LEDs.

This equates to $12 per LED, from which an LED strength of about 8mW each can easily be calculated. Hence, five UVC LEDs at 8mW each is the figure that will be used to determine how fast the Pollux should move.

Recall the figure of 27mW*s per cm² – if we assume that the five LEDs are arranged in a strip such that the length of the underside of the Pollux receives 8mW in a one-centimeter thick band, then the width component of of this figure can be ignored since the Pollux’s navigation should ensure that all area is covered length-wise. Hence, 27mW*s per cm² becomes 8mW*3.375s per cm, or 3.375s per cm based on our circumstances.

One last issue remains – the aforementioned price point applies to UVC LEDs between 265nm and 280nm (assume 270nm for simplicity), whereas an LED of wavelength 222nm is required for the above sanitization speed. A solution to this issue is to simply expose each centimeter of surface to 8mW*3.375s per cm scaled by an appropriate factor, such that each cm receives the same amount of energy as if it were done using 222nm LEDs. Utilizing the formula E = hc / λ, it can be calculated that each photon of 222nm contains 22% more energy than a photon of 270nm. Thus, scaling 3.375s per cm by 1.22 yields 4.1175s per cm. To account for any discrepancies, this number will be bumped up to an even 5 seconds per cm.

Hence, the Pollux will move at 5 seconds per cm to mimic >95% sanitization, given this scenario.

### 6 Cost Breakdown

Project Costs for Production of Beta Version (Next Unit after Prototype)

Item | Quantity | Description | Unit Cost | Extended Cost
1 | 5 | 8mW UV-C Light | $12 | $60
2 | 5 | Ultrasonic sensors | $2 | $10
3 | 1 | Raspberry Pi 4 Model B | $45 | $45
4 | 1 | Lithium Battery | $40 | $40
5 | 2 | Stepper Motors | $3 | $6
6 | 1 | IMU | $15 | $15
7 | 2 | Wheels | $1 | $2

8 | 1 | Caster wheel | $2 | $2
9 | 18 | Magnets | $0.20 | $3.60
10 | 1 | Filament for Housing | $15 | $15
Beta Version Total Cost | | | | $198.60

The most expensive component of our cost estimate is the UV-C light, which is essential for the Pollux to perform its intended sanitation function. While this part was excluded from the alpha version for safety reasons during testing, it remains a necessary expense for the beta version.

The second highest cost is the battery. This larger battery was required to support the combined power demands of the Raspberry Pi running the reinforcement learning model, the UV-C light, and the motors.

Given the original budget and the advanced functionality of the Pollux, the total cost of $198.60 is relatively inexpensive, especially for a custom built, autonomous sanitizing robot with smart navigation capabilities. The use of affordable ultrasonic sensors instead of expensive LiDAR systems was a deliberate design choice to keep costs low.

### 7 Appendices

### 7.1 Appendix A — Specifications

### 7.2 Appendix B — Team Information

Wenhao Cao
Worked on Web control with Karl. Graduating in May 2025
Requirement | Value, range, tolerance, units
Area coverage | 50-60% of total surface area covered at least
Edge avoidance | 100%
Germicidal efficiency | >95% at 5 seconds per cm
User-independence | Minimum 8 hours runtime without need for user interaction.
Gyroscopic sensitivity | Trigger at a tilt greater than 20 degrees.
Function indication | Sanitizing / Non-sanitizing
Durability | Withstand fall from 4 feet (typical countertop height)

Karl Carisme

Louis Cicala
Worked on electronics and documentation. Graduating in December 2025.

Noah Hathout
Worked on ROS, the reinforcement learning model, simulations, testing, debugging, 3D printing. Graduating in May 2025.

Caelan Wong
Worked on the housing design, all the 3D modeling and documentation. Graduating in May 2025.

### 7.3 Appendix C — Text Citations

[1] H. Salonen, T. Salthammer, E. Castagnoli, M. Täubel, and L. Morawska, "Cleaning products: Their chemistry, effects on indoor air quality, and implications for human health," Environment International, vol. 190, 2024, Art. no. 108836. [Online]. Available: https://doi.org/10.1016/j.envint.2024.108836.
[2] Song BM, Lee GH, Han HJ, Yang JH, Lee EG, Gu H, Park HK, Ryu K, Kim J, Kang SM, Tark D. Ultraviolet-C light at 222 nm has a high disinfecting spectrum in environments contaminated by infectious pathogens, including SARS-CoV-2. PLoS One. 2023 Nov 28;18(11):e0294427. doi: 10.1371/journal.pone.0294427. PMID: 38015931; PMCID: PMC10684113.
[3] Kyle D. Rauch, Sean A. MacIsaac, Bailey Reid, Toni J. Mullin, Ariel J Atkinson, Anthony L Pimentel, Amina K. Stoddart, Karl G. Linden, Graham A. Gagnon, A critical review of ultra-violet light emitting diodes as a one water disinfection technology, Water Research X, Volume 25, 2024, 100271, ISSN 2589-9147, https://doi.org/10.1016/j.wroa.2024.100271. (https://www.sciencedirect.com/science/article/pii/S2589914724000616)

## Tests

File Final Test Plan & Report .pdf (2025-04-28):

## Boston University Electrical & Computer Engineering

EC463 Capstone Senior Design Project

## Final Testing Plan & Report

## The Pollux

by Team 22

Wenhao Cao wenhaoc@bu.edu
Karl Carisme karlc@bu.edu
Louis Cicala cicala@bu.edu Noah Hathout nhathout@bu.edu Caelan Wong caewong@bu.edu

Equipment

The Pollux is an autonomous countertop cleaning robot with hardware and software components. Beginning with the hardware, the Pollux is built around a Raspberry Pi and is comprised of the following electronic components:

- Raspberry Pi 4B
- 5 x HR-SC04 Ultrasonic Sensors
- Adafruit MPU-6050 IMU
- 2 x IPSG Step Motor Driver Board + 5V Stepper Motor
- 1 x Green LED “ON/OFF”
- 3 x Red LED “Faux UVC”
- 1 x Orange LED “Indicator”
- 1 x Energizer UE20058 5V 20000mAh Battery Pack

Housing these components is a specially designed 3D-printed chassis, with mounts for the Raspberry Pi, motors, sensors, and the battery pack. Within the top of the chassis are magnets that keep the lid in place whilst also allowing for easy removal and access to the internals of the Pollux. Along with two wheels attached to the motors, on the bottom there is also a caster wheel to allow for stability and easy rotation.

On the software side, the robot’s movements are controlled using the Robotic Operating System (ROS Noetic) running on Ubuntu 20.04, with several ROS nodes dedicated to different tasks. Below is a flowchart detailing each of the ROS nodes, as well as what components each node subscribes to:

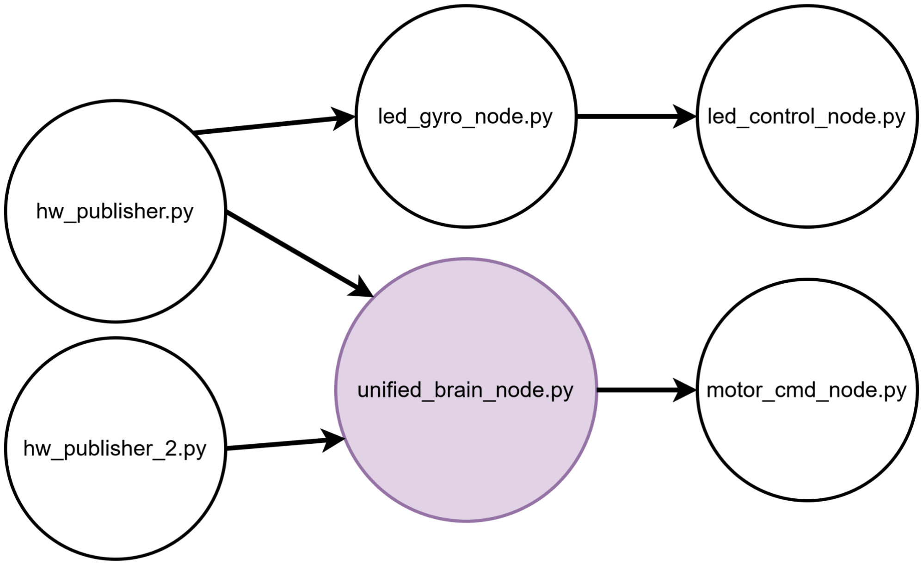
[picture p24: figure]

Below is a brief description of each node:
- hw_publisher.py: Publishes data from the IMU (on ROS topic /pollux/imu) and from the three downward-facing ultrasonic sensors (on /pollux/ultrasonic/hw).
- hw_publisher_2.py: Publishes data from the two forward-facing ultrasonic sensors (on /pollux/ultrasonic_2).
- unified_brain_node.py: Subscribes to the sensor topics published by the hardware nodes (bottom and/or front ultrasonic, plus any IMU data if needed) and decides the appropriate motor commands for navigation or avoidance maneuvers. This logic involves reacting to obstacles, cliffs, or other conditions to ensure safe and effective movement.
- motor_cmd_node.py: Subscribes to the Brain Node for motor command integers (e.g., forward, turn, stop). It then modulates the GPIO pins for each stepper motor, controlling the left and right motor drivers to execute these commands.
- led_gyro_node.py: Subscribes specifically to the IMU data (from the Hardware Nodes) to monitor the robot’s tilt and angular velocity. If the robot’s orientation is deemed unsafe (e.g., too much tilt), this node issues commands (published on /pollux/led_cmd) to turn off the UV-C LED strip for safety.
- led_control_node.py: Receives LED command codes (from the LED Gyro Node or other parts of the system) and drives the actual GPIO pins for the UV-C LEDs, indicator LEDs, and the general “robot on” LED. It serves as the low-level interface to physically turn LEDs on or off in response to higher-level logic.
- Web App: Although not yet fully implemented, reads commands from the web app and publishes them to the motor node

All of these nodes are initialized on boot and begin operation once the Raspberry Pi receives power, following a start-up delay of approximately one minute.

Setup

As just described, the Pollux begins operation on boot. Hence, the only setup required between the hardware and software is to power on the robot. Should our grader wish to see the internals of the robot during testing, the lid may first be removed. For bookkeeping purposes, here is are the GPIO pin connections of each hardware component:

Left Motor Driver | Right Motor Driver
IN1 | 26 | IN1 | 21
IN2 | 19 | IN2 | 20
IN3 | 13 | IN3 | 16

IN4 | 6 | IN4 | 12
Top Left Ultrasonic Sensor | | Top Right Ultrasonic Sensor
Echo | 4 | Echo | 27
Trig | 17 | Trig | 22
Bottom Left Ultrasonic Sensor | | Bottom Middle Ultrasonic Sensor
Echo | 18 | Echo | 24
Trig | 23 | Trig | 25
Bottom Right Ultrasonic Sensor | | AMU Gyroscope / Accelerometer
Echo | 8 | SDA | 2
Trig | 7 | SCL | 3
LEDs | | ON/OFF | 9
Faux UVC | 10 | Indicator | 11

Testing Procedure

In our final testing, we will demonstrate three capabilities of the Pollux in combination with its primary function of mimicked sanitization:
1. Cliff detection
2. Obstacle detection
3. Gyroscopic LED failsafe

Here is a compact testing procedure to analyze these capabilities:
1. Clear off a lab desk and place the Pollux on it
2. Power on the Pollux
3. Allow the Pollux to reach cliffs at least 10 times
a. Measure whether the Pollux stops and turns (✓) or falls (✖)
4. Place obstacles on the desk in front of the Pollux at least 10 times
a. Measure whether the Pollux stops and turns (✓) or collides (✖)
5. While moving, tilt the Pollux upwards and observe the underside at least 5 times
a. Measure whether the bottom LEDs turn off (✓) or stay on (✖)

Score Sheet

Cliff Detection | 1 | 2 | 3 | 4 | 5 | 6 | 7 | 8 | 9 | 10

Pass/Fail

Obstacle Detection | 1 | 2 | 3 | 4 | 5 | 6 | 7 | 8 | 9 | 10

Pass/Fail

Gyroscopic Failsafe | 1 | 2 | 3 | 4 | 5 | 6 | 7 | 8 | 9 | 10

Pass/Fail

Testing Analysis

After some brief debugging prior to our final testing, we were able to successfully demonstrate the capabilities of the Pollux as described above.

Analysis of Functional Requirements

Our client, Jennefer, described the Pollux to us as follows:
“A self-operating countertop cleaning robot that can automatically clean surfaces. It will be able to map out and navigate surfaces to determine an effective pattern to clean them. It should be able to sense when it’s at the edge of a counter and turn in the other direction. It should also be able to avoid obstacles. It contains brushes and a vacuum, allowing it to clean up messes and it will sterilize using UV light, preventing the need for harsh chemicals. It will have a visual indication of what mode it’s on (mapping, cleaning, disinfecting).”
We can break this description down and use it as a metric to analyze completion of the Pollux:
- “A self-operating countertop cleaning robot that can automatically clean surfaces”
The Pollux works without human interaction and traverses countertops to mimic UV sanitization.
- “Able to map out and navigate surfaces to determine an effective pattern to clean them” Soon after we began working on the Pollux, we decided the ability to map out a surface was not only highly complicated, but also unnecessary. Instead, we opted for an adjacent, simpler solution. Currently implemented for navigation is a probabilistic algorithm with a degree of randomness to guide which direction the robot turns when it reaches a cliff or an obstacle. Our more permanent solution, though, is a fully-trained reinforcement learning algorithm designed to navigate more efficiently. While the algorithm is finished and ready to be implemented, we have refrained from implementing it yet due to time restraints. As such, for the final project testing, we instead use our strictly-probabilistic navigation algorithm.

- “Able to sense when it’s at the edge of a counter and turn in the other direction” The Pollux detects cliffs and avoids them.
- “Able to avoid obstacles”
The Pollux detects obstacles and avoids them.
- “Contains brushes and a vacuum, allowing it to clean up messes”
We greatly de-emphasized this function of the Pollux over the duration of our work. Functionally, these components are important to ensure the cleaning capabilities of the Pollux, but from a technical standpoint, they are incredibly simplistic. Therefore, we opted to focus on the more technologically challenging requirements, rather than spend the time developing a custom cleaning system. For this reason, we have yet to implement them, and are considering doing so during customer installation.
- “Sterilize using UV light, preventing the need for harsh chemicals”
The Pollux contains an array of red LEDs on its underside, meant to mimic UVC LEDs capable of sanitization. Generally, UV sanitization can be slow when using low-wattage diodes. Thus, for testing purposes, we have increased the speed of the robot in order to make edge and obstacle detection easier to observe. As a note, the true speed required for 99% sanitization would be hundreds of times slower than we have implemented for testing. We will, however, reduce the robot’s speed back down for customer installation, such that it fits the client’s needs as opposed to what was more beneficial to us during testing.
- “It will have a visual indication of what mode it’s on”
While we did not develop any kind of modal system, as we saw it an unnecessary addition, we have included a green LED to indicate when the robot is on or off, as well as an orange LED to indicate when the faux UVC diodes are active (when the robot is on ‘sanitization mode’).

Feedback

Following our testing, we received a few key pieces of feedback. A minor comment was to include resistors between our LEDs and their voltage source, as they were likely not receiving enough current, dimming them.

A more significant component of our feedback, though, was to implement some form of motion tracking prior to ECE day during our customer installation period. This feedback was given in response to a question raised as to how we track how much of a surface the Pollux would be able to cover. Our solution to this will be to implement our existing reinforcement learning algorithm into our ROS system, which should allow the robot to cover spaces more efficiently.

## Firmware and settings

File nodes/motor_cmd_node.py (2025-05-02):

#!/usr/bin/env python3

"""
motor_cmd_node.py listens to /pollux/motor_cmd for motion commands and translates them into
motor control actions using the DualMotorController module. Executes forward, backward,
turning, spinning, and stopping commands based on numeric codes. Depends on the motors.py
hardware interface and is triggered by brain_node.py
"""

import os, sys, threading, rospy
from std_msgs.msg import Int32

SCRIPT_DIR = os.path.dirname(__file__)
POLLUX_AMR_DIR = os.path.abspath(os.path.join(SCRIPT_DIR, '../../pollux-AMR/hardware'))
if POLLUX_AMR_DIR not in sys.path:
    sys.path.insert(0, POLLUX_AMR_DIR)

import motors

def command_callback(msg):
    """
    Command mapping:
      0 → forward   1 → backward
      2 → turn left 3 → turn right
      4 → spin left 5 → spin right
      6 → stop
      7 → 180° rotate
      8 → slight spin L   9 → slight spin R
    """
    cmd = msg.data
    rospy.loginfo("motor_cmd_node got cmd %d", cmd)

    if   cmd == 0:  # Forward
        # Lower speed from 900 to, say, 500 for a slower forward
        motor_ctrl.move_forward(500, 3)

    elif cmd == 1:  # Backward
        # Also slower
        motor_ctrl.move_backward(500, 3)

    elif cmd == 2:        # gentle turn left 20°
        steps = 400                     # ≈ 1/3 full spin
        t1 = threading.Thread(target=motor_ctrl.motor_left.rotate,  args=(-steps,3))
        t2 = threading.Thread(target=motor_ctrl.motor_right.rotate, args=( steps,3))
        t1.start(); t2.start(); t1.join(); t2.join()

    elif cmd == 3:        # gentle turn right 20°
        steps = 400
        t1 = threading.Thread(target=motor_ctrl.motor_left.rotate,  args=( steps,3))
        t2 = threading.Thread(target=motor_ctrl.motor_right.rotate, args=(-steps,3))
        t1.start(); t2.start(); t1.join(); t2.join()

    elif cmd == 4:  # spin left
        motor_ctrl.motor_left.rotate(-1200,3)
        motor_ctrl.motor_right.rotate( 1200,3)

    elif cmd == 5:  # spin right
        motor_ctrl.motor_left.rotate( 1200,3)
        motor_ctrl.motor_right.rotate(-1200,3)

    elif cmd == 6:  # stop
        pass

    elif cmd == 7:  # 180° rotate
        # Increase the step count for a bigger turn if needed
        t1 = threading.Thread(target=motor_ctrl.motor_left.rotate,  args=(2500,3))
        t2 = threading.Thread(target=motor_ctrl.motor_right.rotate, args=(2500,3))
        t1.start(); t2.start(); t1.join(); t2.join()

    elif cmd == 8:  # slight spin left
        # Increase from 200 to e.g. 1200 steps if you want a 2-second spin
        # (depends on your motor, speed, gear ratio, etc.)
        steps = 1200
        t1 = threading.Thread(target=motor_ctrl.motor_left.rotate,  args=(-steps,3))
        t2 = threading.Thread(target=motor_ctrl.motor_right.rotate, args=( steps,3))
        t1.start(); t2.start(); t1.join(); t2.join()

    elif cmd == 9:  # slight spin right
        steps = 1200
        t1 = threading.Thread(target=motor_ctrl.motor_left.rotate,  args=( steps,3))
        t2 = threading.Thread(target=motor_ctrl.motor_right.rotate, args=(-steps,3))
        t1.start(); t2.start(); t1.join(); t2.join()

    else:
        rospy.logwarn("Unknown motor command %d", cmd)

if __name__ == '__main__':
    rospy.init_node('motor_cmd_node')

    motor_pins = {
        'left':  [6, 13, 19, 26],
        'right': [12, 16, 20, 21],
    }
    motor_ctrl = motors.DualMotorController(motor_pins)

    rospy.Subscriber('/pollux/motor_cmd', Int32, command_callback)
    rospy.loginfo("motor_cmd_node ready.")
    rospy.spin()
    motor_ctrl.cleanup()

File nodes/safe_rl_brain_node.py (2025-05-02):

#!/usr/bin/env python3
"""
safe_rl_brain_node.py  –  PPO + blocking safety shield

Hard-coded shield keeps the robot safe.
Reward now *heavily* discourages any motion that drifts the chassis
backward when no hazard was seen.

CLI
----
rosrun pollux_amr safe_rl_brain_node.py --mode infer
rosrun pollux_amr safe_rl_brain_node.py --mode train --timesteps 200000
rosrun pollux_amr safe_rl_brain_node.py --mode resume --timesteps 40000
"""
# ───────────────────────────────────────────────────────────────────
import argparse, random
from pathlib import Path

import gym, numpy as np, rospy
from gym import spaces
from sensor_msgs.msg import Imu
from std_msgs.msg import Float32MultiArray, Int32
from stable_baselines3 import PPO
from stable_baselines3.common.vec_env import DummyVecEnv, VecMonitor

# ─── topics & motor codes ─────────────────────────────────────────
BOTTOM_T = "/pollux/ultrasonic_hw"
FRONT_T  = "/pollux/ultrasonic_2"
IMU_T    = "/pollux/imu"
CMD_T    = "/pollux/motor_cmd"

FWD, BWD, STOP       = 0, 1, 6
SPIN_L, SPIN_R, ROT  = 4, 5, 7                 # 7 = 180° rotate
ACTION_MAP = {0: FWD, 1: BWD, 2: SPIN_L, 3: SPIN_R, 4: STOP, 5: ROT}

# ─── shield params (from unified_brain_node) ──────────────────────
CLIFF_CM, OBST_CM = 10.0, 12.0
BACK_SEC, ROT_SEC = 2.0, 4.0
SPIN_SEC          = 2.0
CTRL_HZ           = 2                              # agent control rate

# ─── reward tuning ────────────────────────────────────────────────
COVERAGE_BONUS         = 1.2     # reward / 10 cm of novel displacement
BACKWARD_BIG_PENALTY   = 4.0     # ↑ (was 2) – blind straight reverse
UNNEEDED_SPIN_PENALTY  = 1.5     # when both sensors clear
UNNEEDED_ROT_PENALTY   = 3.0
OSCILLATE_PENALTY      = 0.25
STUCK_STEPS            = 4
ROT_AFTER_BWD_BONUS    = 3.0

# ═════════════════ Gym ENV ════════════════════════════════════════
class PolluxEnv(gym.Env):
    metadata = {}
    MAX_CM, ACC_LIM = 100.0, 3.0

    def __init__(self):
        super().__init__()
        self.cmd_pub = rospy.Publisher(CMD_T, Int32, queue_size=4)

        self.bottom = np.zeros(3, np.float32)
        self.front  = np.zeros(2, np.float32)
        self.acc_xy = [0.0, 0.0]

        rospy.Subscriber(BOTTOM_T, Float32MultiArray, self._bottom_cb, queue_size=5)
        rospy.Subscriber(FRONT_T,  Float32MultiArray, self._front_cb,  queue_size=5)
        rospy.Subscriber(IMU_T,    Imu,               self._imu_cb,    queue_size=5)

        self.action_space      = spaces.Discrete(6)
        self.observation_space = spaces.Box(0, 1, (7,), np.float32)
        self.rate = rospy.Rate(CTRL_HZ)

        self.prev_obs = None
        self.prev_act = None
        self.same_obs_ctr = 0

    # ---------- callbacks ----------
    def _bottom_cb(self, msg, *_): self.bottom[:] = np.maximum(msg.data[:3], 0.0)
    def _front_cb(self,  msg, *_): self.front[:]  = np.maximum(msg.data[:2], 0.0)
    def _imu_cb(self,    msg, *_): self.acc_xy[:] = [msg.linear_acceleration.x,
                                                     msg.linear_acceleration.y]

    # ---------- helpers ------------
    def _get_obs(self):
        norm = lambda v: min(v, self.MAX_CM) / self.MAX_CM
        ax_n = min(abs(self.acc_xy[0]), self.ACC_LIM) / self.ACC_LIM
        ay_n = min(abs(self.acc_xy[1]), self.ACC_LIM) / self.ACC_LIM
        return np.array([*map(norm, self.bottom),
                         *map(norm, self.front),
                         ax_n, ay_n], np.float32)

    def _reward(self, act, obs):
        b_cm, f_cm = obs[:3]*self.MAX_CM, obs[3:5]*self.MAX_CM
        cliff = (b_cm > CLIFF_CM).any()
        L, R  = 0 < f_cm[0] < OBST_CM, 0 < f_cm[1] < OBST_CM
        both  = L and R
        clear = not (L or R or both)

        r = 0.0
        # ① hazards
        if cliff:  r -= 10.0
        elif both: r -=  4.0

        # ② single-side correct spin
        if   L and ACTION_MAP[act] == SPIN_R: r += 2.0
        elif R and ACTION_MAP[act] == SPIN_L: r += 2.0

        # ③ back-rotate combo
        if self.prev_act == 1 and ACTION_MAP[act] in {SPIN_L, SPIN_R, ROT}:
            r += ROT_AFTER_BWD_BONUS

        # ④ coverage
        if self.prev_obs is not None:
            delta = np.linalg.norm((obs - self.prev_obs) * self.MAX_CM)
            r += COVERAGE_BONUS * (delta / 10.0)
            self.same_obs_ctr = self.same_obs_ctr + 1 if delta < 2.0 else 0
            if self.same_obs_ctr >= STUCK_STEPS:
                r -= OSCILLATE_PENALTY

        # ⑤ discourage any backwards-drifting motion when sensors are clear
        if ACTION_MAP[act] == BWD and clear:
            r -= BACKWARD_BIG_PENALTY
        if ACTION_MAP[act] in {SPIN_L, SPIN_R} and clear and self.prev_act != 1:
            r -= UNNEEDED_SPIN_PENALTY
        if ACTION_MAP[act] == ROT and clear and self.prev_act != 1:
            r -= UNNEEDED_ROT_PENALTY

        # ⑥ same action tax
        if self.prev_act is not None and act == self.prev_act:
            r -= 0.1

        return r

    # ---------- Gym API -----------
    def reset(self):
        self.cmd_pub.publish(STOP); rospy.sleep(0.2)
        self.prev_obs = self.prev_act = None
        self.same_obs_ctr = 0
        return self._get_obs()

    def step(self, act):
        self.cmd_pub.publish(ACTION_MAP[int(act)])
        self.rate.sleep()
        obs = self._get_obs()
        rew = self._reward(act, obs)
        self.prev_obs, self.prev_act = obs, act
        return obs, rew, False, {}

    def close(self): self.cmd_pub.publish(STOP)

# ═════════════════════ Shield (unchanged) ═════════════════════════
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

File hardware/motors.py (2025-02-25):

# combined motor control stuff.

import RPi.GPIO as GPIO
import time
import threading

class StepperMotor:
    def __init__(self, pins, steps_per_rev=2038):
        self.pins = pins
        self.steps_per_rev = steps_per_rev
        self.step_sequence = [
            [1,0,0,0],
            [1,1,0,0],
            [0,1,0,0],
            [0,1,1,0],
            [0,0,1,0],
            [0,0,1,1],
            [0,0,0,1],
            [1,0,0,1]
        ]
        
        GPIO.setmode(GPIO.BCM)
        GPIO.setup(self.pins, GPIO.OUT)
        
    def rotate(self, steps, rpm):
        delay = 60.0 / (self.steps_per_rev * rpm) / 8
        direction = 1 if steps > 0 else -1
        steps = abs(steps)
        
        for _ in range(steps):
            step_index = _ % 8
            current_step = self.step_sequence[step_index if direction > 0 else 7 - step_index]
            for pin, state in zip(self.pins, current_step):
                GPIO.output(pin, state)
            time.sleep(delay)

class DualMotorController:
    def __init__(self, motor_pins):
        self.motor_left = StepperMotor(motor_pins['left'])
        self.motor_right = StepperMotor(motor_pins['right'])
        
    def move_forward(self, steps, rpm):
        # Run both motor rotates concurrently.
        left_thread = threading.Thread(target=self.motor_left.rotate, args=(-steps, rpm))
        right_thread = threading.Thread(target=self.motor_right.rotate, args=(steps, rpm))
        left_thread.start()
        right_thread.start()
        left_thread.join()
        right_thread.join()
        
    def move_backward(self, steps, rpm):
        self.move_forward(-steps, rpm)
        
    def turn_left(self, degrees, rpm):
        steps = int(degrees * self.motor_left.steps_per_rev / 360)
        self.motor_right.rotate(steps, rpm)
        
    def turn_right(self, degrees, rpm):
        steps = int(degrees * self.motor_left.steps_per_rev / 360)
        self.motor_left.rotate(steps, rpm)
        
    def cleanup(self):
        GPIO.cleanup()

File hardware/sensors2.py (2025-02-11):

import RPi.GPIO as GPIO
import time

# Define GPIO pins for HC-SR04 sensors
# Sensor 1
TRIG1 = 3
ECHO1 = 2
# Sensor 2
TRIG2 = 27
ECHO2 = 17
# Sensor 3
TRIG3 = 9
ECHO3 = 10
# Sensor 4
TRIG4 = 24
ECHO4 = 23

# Set up GPIO
GPIO.setmode(GPIO.BCM)
GPIO.setup([TRIG1, TRIG2, TRIG3, TRIG4], GPIO.OUT)
GPIO.setup([ECHO1, ECHO2, ECHO3, ECHO4], GPIO.IN)

# Function to get the distance for each sensor
def get_distance(trig_pin, echo_pin):
    # Send a pulse to trigger the sensor
    GPIO.output(trig_pin, GPIO.LOW)  # Ensure TRIG is low initially
    time.sleep(0.1)
    GPIO.output(trig_pin, GPIO.HIGH)  # Send trigger pulse
    time.sleep(0.00001)  # 10 microseconds pulse width
    GPIO.output(trig_pin, GPIO.LOW)  # Stop sending pulse
    
    # Measure the duration of the echo pulse
    while GPIO.input(echo_pin) == GPIO.LOW:
        pulse_start = time.time()
    
    while GPIO.input(echo_pin) == GPIO.HIGH:
        pulse_end = time.time()

    # Calculate the distance
    pulse_duration = pulse_end - pulse_start
    distance = pulse_duration * 17150  # Speed of sound in cm/s
    distance = round(distance, 2)  # Round the distance to 2 decimal places
    return distance

try:
    while True:
        for i, (trig, echo) in enumerate([(TRIG1, ECHO1), (TRIG2, ECHO2), (TRIG3, ECHO3), (TRIG4, ECHO4)], 1):
            distance = get_distance(trig, echo)
            print(f"Sensor {i}: Distance = {distance} cm")
            time.sleep(1)  # Delay of 1 second before next measurement
        
except KeyboardInterrupt:
    print("Stopping and cleaning up GPIO.")
    GPIO.cleanup()

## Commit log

2024-11-17 sample ROS2 publisher node added
2025-02-11 BUGFIX updated requirements.txt and added file for controlling hardware
    [hardware_interface.py]
2025-02-13 BUGFIX fixe calling of config file
    [test_ultrasonic.py]
2025-02-13 BUGFIX fixed initialization of mpu6050
    [imu.py]
2025-02-20 BUGFIX pin config & HW tests
    [test_imu.py, test_motors.py, test_ultrasonic.py]
2025-02-20 BUGFIX ultrasonic test
2025-02-24 ADDED brain node, updated motor_cmd_node, and updated the readme to tell users how to run everything
2025-02-24 BUGFIX fixed brain node and motor cmd node to hopefully fix buggy motors
    [brain_node.py, motor_cmd_node.py]
2025-02-24 BUGFIX tried to increase amount fo steps for the motors
    [motor_cmd_node.py]
2025-02-24 BUGFIX tried to increase rpm for the motors
    [motor_cmd_node.py]
2025-02-24 ADDED more motor controls
2025-02-24 BUGFIX going back a commit because motors stopped working
    [brain_node.py, motor_cmd_node.py, motors.py]
2025-02-24 BUGFIX turns out it did work
    [brain_node.py, motor_cmd_node.py, motors.py]
2025-02-24 led_gyro_node updates
2025-02-25 BUGFIX negated steps of right motor to fix opposing directions
    [motors.py]
2025-02-25 BUGFIX turns out it was the other motor...
    [motors.py]
2025-02-25 BUGFIX 180 spin was not spinning
    [motor_cmd_node.py]
2025-02-25 BUGFIX increased the cliff threshold
    [brain_node.py]
2025-02-25 BUGFIX fixed cliff threshold, debounce max, and the amount the motors move forward
    [brain_node.py, motor_cmd_node.py]
2025-02-25 BUGFIX slowed motors further
    [motor_cmd_node.py]
2025-03-21 ENHANCEMENT added led control node and led gyro node for led control
2025-03-21 ENHANCEMENT completed nodes for front facing us sensors, waiting for testing
2025-03-28 BUGFIX changed duration of backwards movement (dont want robot falling backwards)
    [brain_node.py]
2025-04-05 BUGFIX updated pin config
    [motor_cmd_node.py]
2025-04-05 BUGFIX motors were coded wrong direction
    [motor_cmd_node.py]
2025-04-05 BUGFIX brain node and hw_publisher bugs
    [brain_node.py, hw_publisher.py]
2025-04-05 BUGFIX fixed motor pins
    [motor_cmd_node.py]
2025-04-06 BUGFIX led control and led gyro nodes
    [led_control_node.py, led_gyro_node.py]
2025-04-06 BUGFIX led control and gyro nodes fixed'
    [led_control_node.py, led_gyro_node.py]
2025-04-06 BUGFIX imu topic not supplying sufficient gyro data
    [led_gyro_node.py]
2025-04-07 BUGFIX GPIO pin conflict
    [led_control_node.py, ultrasonic.py]
2025-04-07 BUGFIX clean up GPIO pins
    [led_control_node.py]
2025-04-07 BUGFIX restored to working hw_publisher.py
    [hw_publisher.py]
2025-04-07 BUGFIX updated slowly with main
    [brain_node.py, motor_cmd_node.py]
2025-04-07 DEBUG change topic name to ultrasonic_hw
2025-04-07 BUGFIX changed topic name to ultrasonic_hw
    [brain_node.py, hw_publisher.py]
2025-04-07 BUGFIX changed the topic names to ultrasonic_hw
    [brain_node.py, hw_publisher.py]
2025-04-07 BUGFIX highered the tilt limit
    [led_gyro_node.py]
2025-04-07 ENHANCEMENT front facing sensors should work now
2025-04-07 BUGFIX top sensors were not working due to calling the wrong config
    [hw_publisher_2.py]
2025-04-07 BUGFIX front facing sensors and unified brain node a bit faulty
    [unified_brain_node.py]
2025-04-07 BUGFIX enhanced unified brain since it would not work @ obstacle/cliff detections
    [unified_brain_node.py]
2025-04-07 BUGFIX increased thresholds in unified_brain & updated hw_publsiher2
    [hw_publisher_2.py, unified_brain_node.py]
2025-04-08 BUGFIX stepper motor step size
    [motor_cmd_node.py]
2025-04-08 BUGFIX fixed pile up of movemnet commands
    [unified_brain_node.py]
2025-04-08 BUGFIX go back to unified brain that worked
    [unified_brain_node.py]
2025-04-08 BUGFIX cliff backwards threshold increased
    [unified_brain_node.py]
2025-04-08 BUGFIX backwards time from cliff
    [unified_brain_node.py]
2025-04-08 BUGFIX spinning on repeat
    [led_gyro_node.py, unified_brain_node.py]
2025-04-18 BUGFIX fixed requirements & pretrained model
    [rl_brain_node.py]
2025-04-18 BUGFIX I shouldnt have changed the model path
    [rl_brain_node.py]
2025-04-18 ENHANCEMENT added IMU integration for punishments
2025-04-18 BUGFIX failed after 1000 iters due to not saving correctly
    [rl_brain_node.py]
2025-04-22 BUGFIX tilt threshold increased, and rl brain fixes
    [led_gyro_node.py, rl_brain_node.py]
2025-04-22 BUGFIX RL model still doesnt save
    [rl_brain_node.py]
2025-04-23 ENHANCEMENT fixed comments at top of rl_brain_node.py
    [rl_brain_node.py]
2025-04-24 BUGFIX not enough spin reward
    [rl_brain_node.py]
2025-04-24 BUGFIX not enough punishment for seeing a cliff
    [rl_brain_node.py]
2025-04-24 BUGFIX highered reward for spinning after seeing a cliff
    [rl_brain_node.py]
2025-04-27 hardware_readme changes
    [Battery_mount.step, Final_housing.step, IMU_mount.step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]
2025-04-30 BUGFIX increased cliff thresh
    [safe_rl_brain_node.py]
2025-04-30 BUGFIX in safe rl brain
    [safe_rl_brain_node.py]
2025-05-01 BUGFIX model didnt save correctly
    [safe_rl_brain_node.py]
2025-05-01 BUGFIX the motor control to better work with the RL
    [motor_cmd_node.py]
2025-05-01 BUGFIX safe rl brain
    [led_gyro_node.py, safe_rl_brain_node.py]
2025-05-01 BUGFIX to hw_publisher, crashes after a bit
    [hw_publisher.py]
2025-05-02 BUGFIX led gyro thresh for angular velocity
    [led_gyro_node.py]
2025-05-02 BUGFIX increased reward for coverage
    [safe_rl_brain_node.py]
2025-05-02 BUGFIX changed name of final model saved
    [safe_rl_brain_node.py]
2025-05-02 BUGFIX lowered coverage bonus
    [safe_rl_brain_node.py]
